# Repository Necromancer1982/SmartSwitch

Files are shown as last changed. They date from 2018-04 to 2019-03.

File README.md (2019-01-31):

# SmartSwitch
## Flush-mounted Module to control shutters / realize an intermediate switch with ESP8266

**Version History**

- SmartSwitch V1.2  04/2018   1st official public Version
- SmartSwitch V1.3  05/2018   ADD: Additional Fuse (F2, 4A) for consumer current
- **Software now avaliable for ArduinoIDE (including OTA)**

**Vision**

During the construction of our new house, we’ve decided to install motorized roller shutters. To control them, we first used only standard shutter-push-buttons, right beside the correspondent window. As second step a *smart solution* should be established.

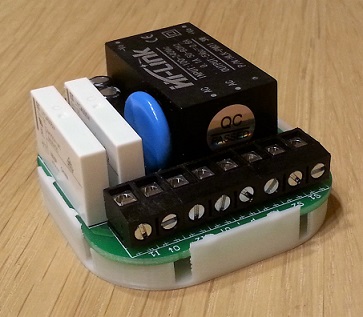
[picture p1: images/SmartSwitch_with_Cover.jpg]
SmartSwitch Modul
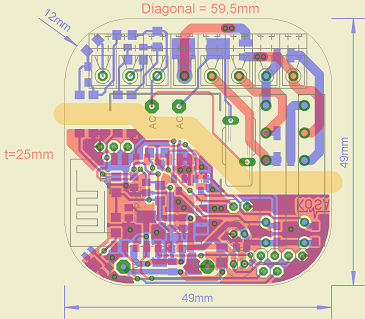
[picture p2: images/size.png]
SmartSwitch Sizing
   

Inspired by Leo-Andres Hofmann’s “230V I/O Modul für ESP8266” ([LUANI](https://luani.de/projekte/esp8266-hvio/)), I’ve decided to develop my own module to sense the shutter-push-buttons and control the motorization.
By its dimensions, the module perfectly fits into a standard round In-Wall-Pattress (inner diameter: 60mm). If its a so called "deep" pattress, the shutter-push-buttons can also be installed on top of the module and there is enough space left for wires and terminals.

Basis of the module is a ESP-12F, an integrated WLAN-Module which controls two changeover relays to move the shutters. 

The operation of the module can either be controlled by the already existing push-buttons, or via MQTT-Messages by WLAN, central controlled via [OpenHab2](https://docs.openhab.org/index.html), running on my Raspberry Pi Zero W. Therefore, a movement of the shutters regarding time or special events, for example time of dusk and down ([Astro Bindings](https://docs.openhab.org/addons/bindings/astro/readme.html)) can be realized. Also an automatized shadowing regarding sun position, global radiation and inside / outside temperature will be possible.

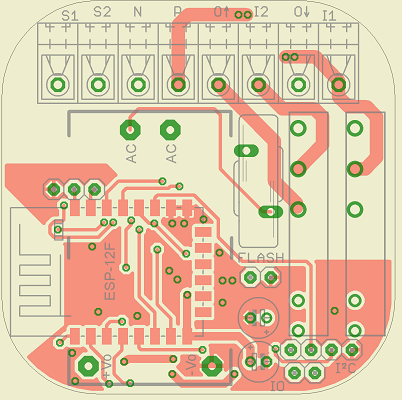
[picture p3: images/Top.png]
PCB Top
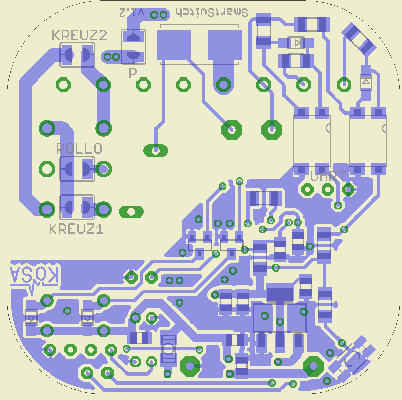
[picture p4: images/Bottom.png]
PCB Bottom
   

**Hardware**

Beside the WLAN-Module and the relays (contact rating 1500VA, 6A/250V), a power supply consisting of a AC/DC-Converter HI-Link HLK-PM01 (5V/600mA) to serve the relays and a voltage regulator TS1117 (LowDrop 3V) to serve the remaining circuit, a 2-chanel power sense circuit to detect 230V levels for the controller and interfaces like UART, I²C and analog/digital IO are included on the board. A push button for hardware reset is also implemented on bottom side of the PCB.

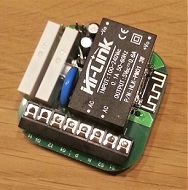
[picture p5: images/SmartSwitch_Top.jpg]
SmartSwitch Modul
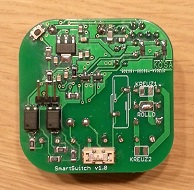
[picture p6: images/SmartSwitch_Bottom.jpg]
SmartSwitch Modul
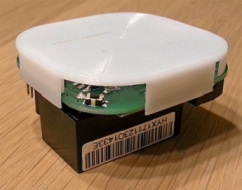
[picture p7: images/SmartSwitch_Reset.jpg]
SmartSwitch Modul
          

Three soldering jumpers give the opportunity to decide if the relays should act as an intermediate switch to implement the module in an already existing light-installation or to act as a roller-shutter-controlling device. Therefore, the first relay powers the motor during the second relay controls moving direction. Via a fourth soldering Jumper it is possible to supply mains voltage to the relays, so for roller shutter function, there is no need to connect phase two times, for supplying the module and supplying the motor. 

The power supply of the module is secured by a SMD-Fuse (500mA) and a varistor (275V) against overload.

**Software**

In addition to the firmware ([NodeMCU](https://nodemcu.readthedocs.io/en/master/)) there are mainly four LUA-Scripts on the Module.

The Init-File tries to connect to the access point whose SSID and password is stored at the ESP. If the connection couldn’t be established, the ESP himself opens an access point and starts an end user setup to give the user the possibility to enter SSID and password of an already existing access point (Router).

If the connection is established, two more software modules will be started. The MQTT-Module starts to configure the implemented MQTT-Client, opens a connection to the MQTT-Broker which is defined (IP, Port) in the MQTT.ini file and provides several procedures for MQTT communication. The INI-Handling-Module provides two more procedures for easy INI-File access by using “Key” and “Value” data.

Finally, the main program will be started.

:+1: _UPDATE_

Now I'd also written a new software for ArduinoIDE.
The main advantage of this new sketch is the possibility of updating the software via OTA (Over the Air update via WiFi).
After flashing the sketch via serial adapter for the first time, the module can be found and flashed via ArduinoIDE OTA-Functionality.

Additionally there are a few smaller upgrades and BugFixes implemented in the new software.

The functionality of the Arduino-Software is mostly the same as the LUA-Skript.
The module tries to connect to the last stored access point. If no connection could be established the module starts its implemented enduser setup. SSID and password of the AP and also the site of usage and MQTT-borker IP can be configured. After this initialisation the module starts its normal operation and can be either controlled via the already existing push buttons or MQTT-Commands.

**Function**

During normal operation, the main program offers the opportunity to control the module via the shutter-push-buttons by using both of the power sense inputs. (Only LUA-Skript: If both buttons were pushed synchronously the module changes to teaching mode.) Via MQTT-Command "TEACH", the module changes to teaching mode. Because of the fact that simple shutter motors neither feedback their position nor the state of their limit switches, the position of the shutter can only be traced by the time, the motor is in motion. Therefore, in teaching mode, the time to reach both final positions can be stored in module by closing and reopening the shutter completely.
After that, a short push of a button results in moving to respective end position. If the button will be pressed longer then 1s the shutter moves as long as the button is pressed or final position is reached. By releasing the button, the current position of the shutter will be calculated regarding the time, the motor was in motion and will be stored in the module. Thus offers the opportunity to start motion from any position of the shutter or moving the shutter to a particular position (e.g. closing until only shutter slots are open).

But not only manual operation by pushing a button is possible. As mentioned, the module acts also as a MQTT-Client. Via messages to the MQTT-Topic (LUA-Skript: which is also settled in MQTT.ini file; ARDUINO-Skript: /SmartSwitch/SmartSwitch_\<SITE or MAC\>/), motion to the final position is possible, either by command “UP” or “DOWN”. By sending a value from 0 to 100 the shutter moves to the correspondent position in percent. If the desired position is reached or the shutter reaches end position, the current position will be also send as MQTT-Message to the broker (ARDUINO: Also the RSSI of the module will be sent). Therefore, a visualization of the current position e.g. with  [HabPanel von OpenHab](https://docs.openhab.org/addons/uis/habpanel/readme.html) is possible.

**Safety**

By operating the module at mains voltage, the active parts and pins should be covered against directly and indirectly touching. Therefore, I’ve designed a Bottom-Coverage ([Project at Thingiverse](https://www.thingiverse.com/thing:3085953)) for the module with FreeCAD and printed it with my Anet A6 3D-Printer. As positive side effect of the coverage, all SMT-Components on bottom side are protected against mechanical damages.

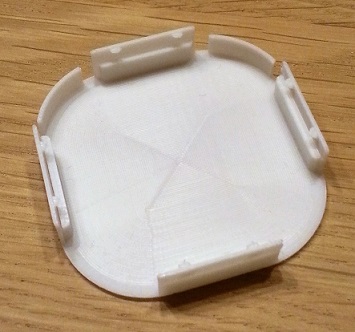
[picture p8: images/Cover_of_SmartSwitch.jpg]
SmartSwitch Modul


### Safety Disclaimer

Building and usage at your own risk. SmartSwitch uses potentially lethal mains voltages.

If you are a beginner in electronics or don't have the proper experience to work with mains voltage, consult a professional! I am not liable for any mishaps that may occur due to misuse of SmartSwitch or electrical system (including mains power) including but not limited to: errors or omissions, loss of life, or property damage. Take all safety precautions as necessary. You are fully responsible for your actions, perform them at your own risk!

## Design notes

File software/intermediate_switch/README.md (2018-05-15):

# SmartSwitch
## Flush-mounted Module to control shutters / realize an intermediate switch with ESP8266

# Software for intermediate switch under construction!

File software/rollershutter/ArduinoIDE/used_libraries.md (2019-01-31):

## Used Libraries for ArduinoIDE

| Library | Link |
|---|---|
| ESP8266WiFi.h | [https://github.com/esp8266/Arduino/tree/master/libraries/ESP8266WiFi](https://github.com/esp8266/Arduino/tree/master/libraries/ESP8266WiFi) |
| WiFiClient.h | [https://github.com/esp8266/Arduino/tree/master/libraries/ESP8266WiFi](https://github.com/esp8266/Arduino/tree/master/libraries/ESP8266WiFi) |
| EEPROM.h | [https://github.com/esp8266/Arduino/tree/master/libraries](https://github.com/esp8266/Arduino/tree/master/libraries) |
| WiFiManager.h | [https://github.com/tzapu/WiFiManager](https://github.com/tzapu/WiFiManager) |
| ArduinoOTA.h | [https://github.com/esp8266/Arduino/tree/master/libraries](https://github.com/esp8266/Arduino/tree/master/libraries) |
| ESP8266mDNS.h | [https://github.com/esp8266/Arduino/tree/master/libraries](https://github.com/esp8266/Arduino/tree/master/libraries) |
| WiFiUdp.h | [https://github.com/esp8266/Arduino/tree/master/libraries/ESP8266WiFi](https://github.com/esp8266/Arduino/tree/master/libraries/ESP8266WiFi)|
| PubSubClient.h | [https://github.com/knolleary/pubsubclient](https://github.com/knolleary/pubsubclient)|
| user_interface.h | [https://github.com/esp8266/Arduino/tree/master/tools/sdk/include](https://github.com/esp8266/Arduino/tree/master/tools/sdk/include)|

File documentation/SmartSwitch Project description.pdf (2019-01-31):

# SmartSwitch

## Flush-mounted Module to control shutters / realize an intermediate switch with ESP8266

Version History

- SmartSwitch V1.2 04/2018 1st official public Version
- SmartSwitch V1.3 05/2018 ADD: Additional Fuse (F2, 4A) for consumer current
- Software now avaliable for ArduinoIDE (including OTA)

Vision

During the construction of our new house, we’ve decided to install motorized roller shutters. To control them, we first used only standard shutter-push-buttons, right beside the correspondent window. As second step a smart solution should be established.

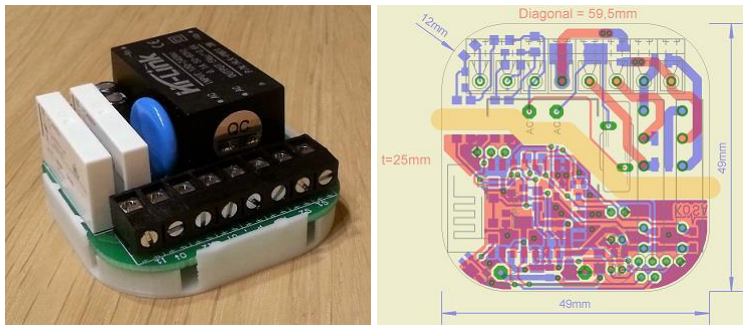
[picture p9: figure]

Inspired by Leo-Andres Hofmann’s “230V I/O Modul für ESP8266” (LUANI), (https://luani.de/projekte/esp8266-hvio/) I’ve decided to develop my own module to sense the shutter-push-buttons and control the motorization. By its dimensions, the module perfectly fits into a standard round In-Wall-Pattress (inner diameter: 60mm). If its a so called "deep" pattress, the shutterpush-buttons can also be installed on top of the module and there is enough space left for wires and terminals.

Basis of the module is a ESP-12F, an integrated WLAN-Module which controls two changeover relays to move the shutters.

The operation of the module can either be controlled by the already existing push-buttons, or via MQTT-Messages by WLAN, central controlled via OpenHab2, (https://docs.openhab.org/index.html) running on my Raspberry Pi Zero W. Therefore, a movement of the shutters regarding time or special events, for example time of dusk and down (Astro Bindings) (https://docs.openhab.org/addons/bindings/astro/readme.html) can be realized.

Also an automatized shadowing regarding sun position, global radiation and inside / outside temperature will be possible.

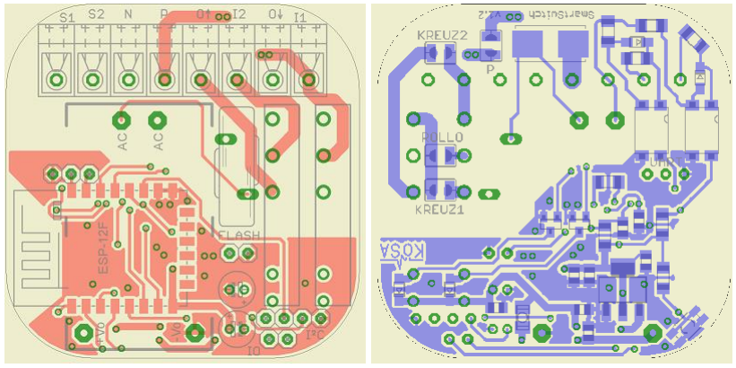
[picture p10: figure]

Hardware

Beside the WLAN-Module and the relays (contact rating 1500VA, 6A/250V), a power supply consisting of a AC/DC-Converter HI-Link HLK-PM01 (5V/600mA) to serve the relays and a voltage regulator TS1117 (LowDrop 3V) to serve the remaining circuit, a 2-chanel power sense circuit to detect 230V levels for the controller and interfaces like UART, I²C and analog/digital IO are included on the board. A push button for hardware reset is also implemented on bottom side of the PCB.

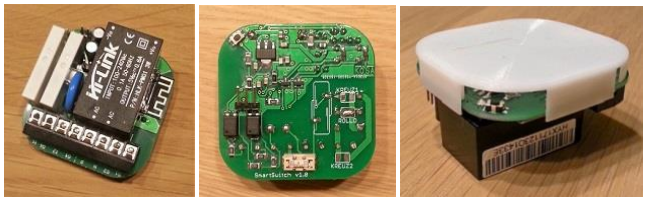
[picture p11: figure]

Three soldering jumpers give the opportunity to decide if the relays should act as an intermediate switch to implement the module in an already existing light-installation or to act as a roller-shutter-controlling device. Therefore, the first relay powers the motor during the second relay controls moving direction. Via a fourth soldering Jumper it is possible to supply mains voltage to the relays, so for roller shutter function, there is no need to connect phase two times, for supplying the module and supplying the motor.

The power supply of the module is secured by a SMD-Fuse (500mA) and a varistor (275V) against overload.

Software

In addition to the firmware (NodeMCU) (https://nodemcu.readthedocs.io/en/master/) there are mainly four LUA-Scripts on the Module.

The Init-File tries to connect to the access point whose SSID and password is stored at the ESP. If the connection couldn’t be established, the ESP himself opens an access point and starts an end user setup to give the user the possibility to enter SSID and password of an already existing access point (Router).

If the connection is established, two more software modules will be started. The MQTT-Module starts to configure the implemented MQTT-Client, opens a connection to the MQTT-Broker which is defined (IP, Port) in the MQTT.ini file and provides several procedures for MQTT communication. The INI-Handling-Module provides two more procedures for easy INI-File access by using “Key” and “Value” data.

Finally, the main program will be started.

👍 UPDATE

Now I'd also written a new software for ArduinoIDE. The main advantage of this new sketch is the possibility of updating the software via OTA (Over the Air update via WiFi). After flashing the sketch via serial adapter for the first time, the module can be found and flashed via ArduinoIDE OTA-Functionality.

Additionally there are a few smaller upgrades and BugFixes implemented in the new software.

The functionality of the Arduino-Software is mostly the same as the LUA-Skript. The module tries to connect to the last stored access point. If no connection could be established the module starts its implemented enduser setup. SSID and password of the AP and also the site of usage and MQTT-borker IP can be configured. After this initialisation the module starts its normal operation and can be either controlled via the already existing push buttons or MQTT-Commands.

Function

During normal operation, the main program offers the opportunity to control the module via the shutter-push-buttons by using both of the power sense inputs. (Only LUA-Skript: If both buttons were pushed synchronously the module changes to teaching mode.) Via MQTT-Command "TEACH", the module changes to teaching mode. Because of the fact that simple shutter motors neither feedback their position nor the state of their limit switches, the position of the shutter can only be traced by the time, the motor is in motion. Therefore, in teaching mode, the time to reach both final positions can be stored in module by closing and reopening the shutter completely. After that, a short push of a button results in moving to respective end position. If the button will be pressed longer then 1s the shutter moves as long as the button is pressed or final position is reached. By releasing the button, the current position of the shutter will be calculated regarding the time, the motor was in motion and will be stored in the module. Thus offers the opportunity to start motion from any position of the shutter or moving the shutter to a particular position (e.g. closing until only shutter slots are open).

But not only manual operation by pushing a button is possible. As mentioned, the module acts also as a MQTT-Client. Via messages to the MQTT-Topic (LUA-Skript: which is also settled in MQTT.ini file; ARDUINO-Skript: /SmartSwitch/SmartSwitch_<SITE or MAC>/), motion to the final position is possible, either by command “UP” or “DOWN”. By sending a value from 0 to 100 the shutter moves to the correspondent position in percent. If the desired position is reached or the shutter reaches end position, the current position will be also send as MQTT-Message to the broker (ARDUINO: Also the RSSI of the module will be sent). Therefore, a visualization of the current position e.g. with HabPanel von OpenHab (https://docs.openhab.org/addons/uis/habpanel/readme.html) is possible.

Safety

By operating the module at mains voltage, the active parts and pins should be covered against directly and indirectly touching. Therefore, I’ve designed a Bottom-Coverage for the module with FreeCAD and printed it with my Anet A6 3D-Printer. As positive side effect of the coverage, all SMT-Components on bottom side are protected against mechanical damages.

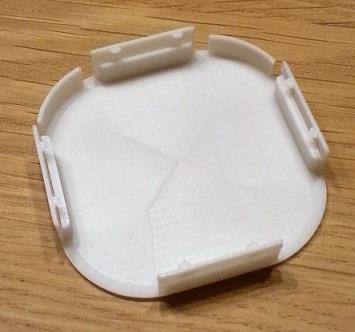
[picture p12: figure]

### Safety Disclaimer

Building and usage at your own risk. SmartSwitch uses potentially lethal mains voltages.

If you are a beginner in electronics or don't have the proper experience to work with mains voltage, consult a professional! I am not liable for any mishaps that may occur due to misuse of SmartSwitch or electrical system (including mains power) including but not limited to: errors or omissions, loss of life, or property damage. Take all safety precautions as necessary. You are fully responsible for your actions, perform them at your own risk!

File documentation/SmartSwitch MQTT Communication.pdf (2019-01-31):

# SmartSwitch MQTT-Communication

## MQTT-Topics:

Topic to send commands to module:
LUA-Script: | /SmartSwitch/<MAC>/command
ARDUINO-Script: /SmartSwitch/SmartSwitch_<SITE or MAC>/command

Topic, the module feedbacks position / RSSI to:
LUA-Script: | /SmartSwitch/<MAC>/status
ARDUINO-Script: /SmartSwitch/SmartSwitch_<SITE or MAC>/status/position /SmartSwitch/SmartSwitch_<SITE or MAC>/status/rssi

## MQTT-Commands:

UP
Opens roller shutter completely and feedbacks position (0) when end position is reached

DOWN
Closes roller shutter completely and feedbacks position (100) when end position is reached

STOP
Stops moving roller shutter and feedbacks current position

[Integer: 0 – 100]
Moves roller shutter to the integer related position in percent and feedbacks reached position

STATUS
Feedbacks current position of roller shutter

TEACH
Sets Module in teaching mode; Moving to lower end position, followed by moving to upper end position, by pressing manual roller shutter buttons, stores time for up-/down-movement into the module

MANUAL_START
Starts “Position-Repair-Mode”; Movement of roller shutter by pressing manual roller shutter buttons is now possible, without storage of position in module after stopping

MAUAL_STOP
Stops “Position-Repair-Mode”

## MQTT-Setup:

Quality of Service Level: | 1
Retain active: | no
Secure active: | no
Keep-alive Time: | 120s

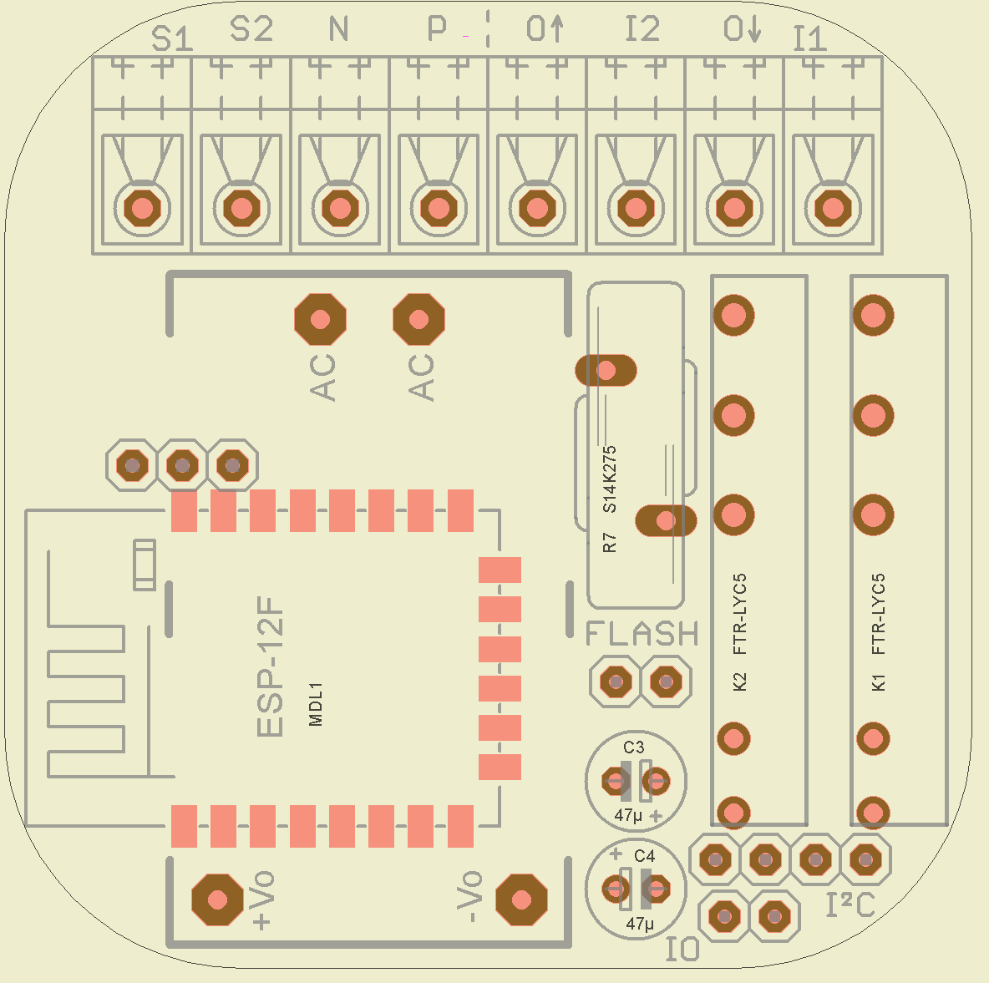
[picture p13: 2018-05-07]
hardware/v1.3/Placing_Top_V1_3.png

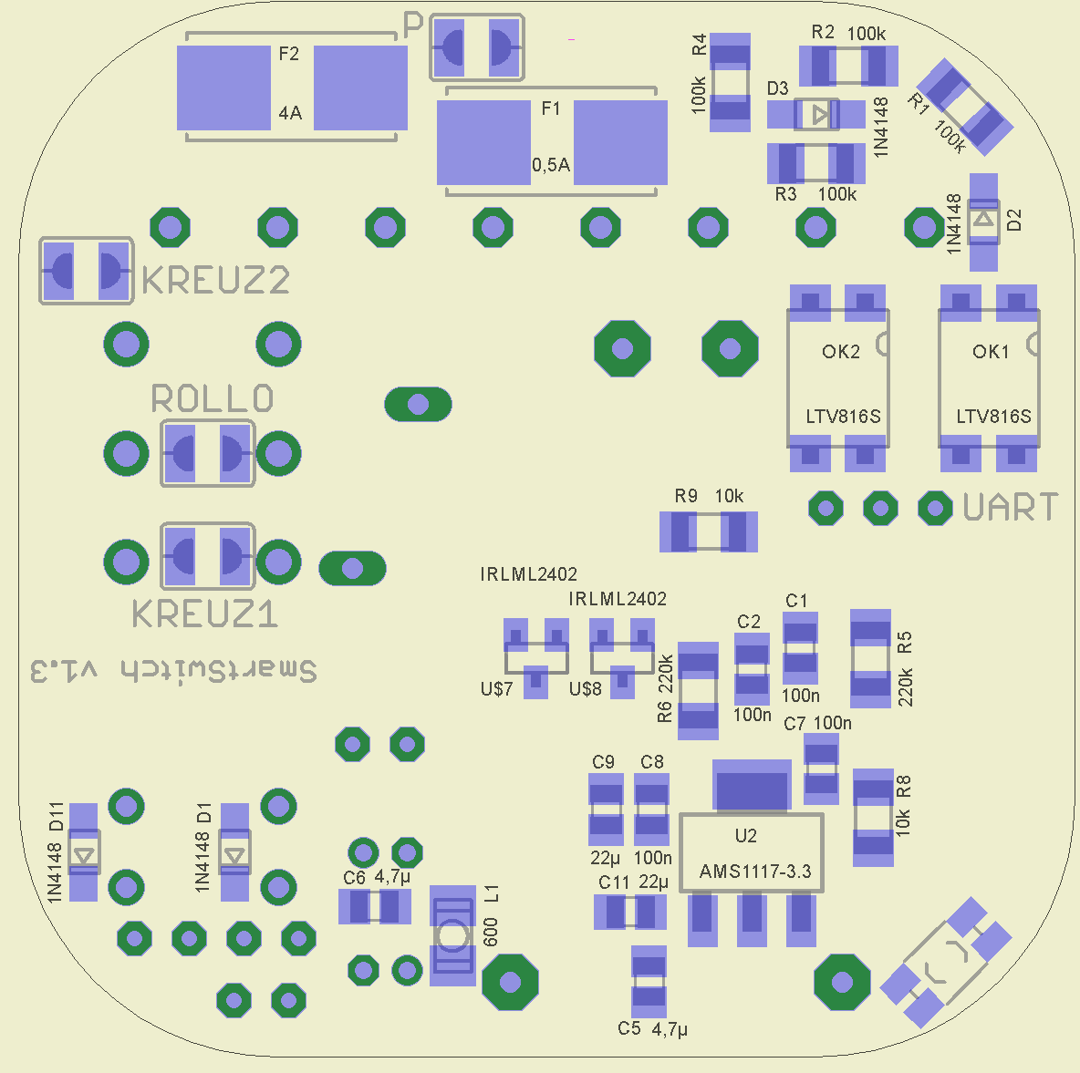
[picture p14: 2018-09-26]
hardware/v1.3/Placing_Bottom_V1_3.png

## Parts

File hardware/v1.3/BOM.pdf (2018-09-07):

Device | Parts | Alternative
1 | PCB | 1,22 € | 1,22 €
1 | SMD-HASF 0,5A | F1 | 0,99 € | 0,99 €
1 | SMD-HASF 4,0A | F2 | 0,99 € | 0,99 €
1 | MDL1 | 3,85 € | 3,85 € | 1,49 €
4 | RND 1206 1 100K | R1, R2, R3, R4 | 0,02 € | 0,08 €
4 | KEM X7R0805 100N | C1, C2, C7, C8 | 0,02 € | 0,08 €
2 | RND 1206 1 10K | R8, R9 | 0,02 € | 0,04 €
4 | 1N 4148 WS | D1, D11 | 0,03 € | 0,12 €
2 | RND 205-00632 | FLASH, IO | 0,05 € | 0,10 €
2 | X5R-G0805 22/6 | C9, C11 | 0,07 € | 0,14 €
1 | RND 205-00624 | UART | 0,11 € | 0,11 €
1 | RND 205-00625 | I²C | 0,08 € | 0,08 €
2 | X7R 0805 CC 4,7U | C5, C6 | 0,04 € | 0,08 €
2 | RND 1206 1 220K | R5, R6 | 0,02 € | 0,04 €
2 | RAD FR 47/25 | C3, C4 | 0,14 € | 0,28 €
1 | BLM31PG 601 | L1 | 0,22 € | 0,22 €
1 | TS 1117 BCW33 | U2 | 0,32 € | 0,32 €
2 | FTR LYCA 005V | K1, K2 | 1,90 € | 3,80 €
1 | Amazon U$1 | 3,98 € | 3,98 € | 1,87 €
2 | IRLML 2402 | U$7, U$8 | 0,16 € | 0,32 €
2 | LTV 816S | OK1, OK2 | 0,22 € | 0,44 €
1 | RND 205-00282 | U$2, U$3, U$4, U$5 | 0,96 € | 0,96 €
1 | VDR-0,6 270 | R7 | 0,21 € | 0,21 €
1 | KMR 231 G LFS | RST | 0,25 € | 0,25 €
17,48 € | 13,24 €

# BOM SmartSwitch V1.3

Qty | Order Number | Supplier | Unit Price | Sum Price
PCB (https://www.itead.cc/open-pcb/pcb-prototyping/2layer-green-pcb-5cm-x-5cm-max.html) | Itead
SMD-HASF 0,5A (SMT-Sicherung inkl. Halter) (https://www.reichelt.de/SMD-Sicherungen/SMD-HASF-0-5A/3/index.html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) | Reichelt
SMD-Sicherung mit Halter, superflink, 4,0A (https://www.reichelt.de/SMD-Sicherungen/SMD-HASF-4-0A/3/index.html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) | Reichelt
AI-Thinker ESP8266 ESP-12F WiFi/WLAN Modul (http://www.watterott.com/de/ESP8266-ESP-12F-WiFi/WLAN-Modul) | Waterott | Aliexpress
SMD-Widerstand, 1206, 100 kOhm, 250 mW, 1% (https://www.reichelt.de/SMD-1206-von-1-bis-910-kOhm/RND-1206-1-100K/3/index.html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) | Reichelt
Vielschicht-Kerko, 100nF, 50V, 125°C (https://www.reichelt.de/Vielschicht-SMD-G0805/KEM-X7R0805-100N/3/index.html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) | Reichelt
SMD-Widerstand, 1206, 10 kOhm, 250 mW, 1% (https://www.reichelt.de/SMD-1206-von-1-bis-910-kOhm/RND-1206-1-10K/3/index.html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) | Reichelt
SMD-Si-Allzweckdioden, SOD323F, 75V, 0,15A (https://www.reichelt.de/1N-UF-AA-Dioden/1N-4148-WS/3/index.html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) | Reichelt
RND Stiftleiste, 2-pol, RM 2,54 mm (https://www.reichelt.de/Stiftleisten/RND-205-00632/3/index.html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) | Reichelt
SMD-Vielschichtkondensator G0805 - 22µF 6,3V (https://www.reichelt.de/Vielschicht-SMD-G0805/X5R-G0805-22-6/3/index.html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) | Reichelt
RND Stiftleiste, 3-pol, RM 2,54 mm (https://www.reichelt.de/Stiftleisten/RND-205-00624/3/index.html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) | Reichelt
RND Stiftleiste, 4-pol, RM 2,54 mm (https://www.reichelt.de/Stiftleisten/RND-205-00625/3/index.html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) | Reichelt
SMD-Kerko, 0805, 4,7µF, 10V, 10%, MLCC (https://www.reichelt.de/Vielschicht-SMD-G0805/X7R-0805-CC-4-7U/3/index.html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) | Reichelt
SMD-Widerstand, 1206, 220 kOhm, 250 mW, 1% (https://www.reichelt.de/RND-1206-1-220K/3/index.html?ACTION=3&LA=55&ARTICLE=183413) | Reichelt
Elko radial, 47 uF, 25 V, 105°C, low ESR (https://www.reichelt.de/Elkos-radial-105-C-5000-10000h/RAD-FR-47-25/3/index.html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) | Reichelt
EMI Suppression Filter SMD1206 BLM31 600 Ohm (https://www.reichelt.de/Filter/BLM31PG-601/3/index.html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) | Reichelt
LDO-U-Reg 3,3V 0,8A SOT223 (https://www.reichelt.de/ICs-TLC-TSA-/TS-1117-BCW33/3/index.html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) | Reichelt
Schmales Netzrelais FTR-LYCA, 5V, 1 We., 6A (https://www.reichelt.de/Print-Steckrelais/FTR-LYCA-005V/3/index.html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) | Reichelt
HI-Link HLK-PM01 AC-DC (https://www.amazon.de/HI-Link-HLK-PM01-Step-Down-Netzteil-Intelligent/dp/B01768OJMS) | Aliexpress
SMD-MOSFET, N-LogL, SOT23, 20V, 1.2A (https://www.reichelt.de/IRL-IRFZ-Transistoren/IRLML-2402/3/index.html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) | Reichelt
Optokoppler 5kV 80V 50mA >50% SMD (https://www.reichelt.de/Optokoppler/LTV-816S/3/index.html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) | Reichelt
Lötbare Schraubklemme - 8-pol, RM 5 mm, 0° (https://www.reichelt.de/RND-connect/RND-205-00282/3/index.html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) | Reichelt
Varistor,Rm 7,5mm, 0,6W, 275VAC (https://www.reichelt.de/Heissleiter-Varistoren/VDR-0-6-270/3/index.html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) | Reichelt
SMD-Kurzhubtaster, 4,2 x 2,8 mm, Höhe 1,9 mm (https://www.reichelt.de/Kurzhubtaster/KMR-231-G-LFS/3/index.html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) | Reichelt

Reichelt Order list (https://www.reichelt.de/my/1501969)

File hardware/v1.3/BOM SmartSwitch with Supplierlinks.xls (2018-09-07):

BOM SmartSwitch V1.3
Qty | Device | Order Number | Supplier | Parts | Unit Price | Sum Price | Alternative
1 | PCB (https://www.itead.cc/open-pcb/pcb-prototyping/2layer-green-pcb-5cm-x-5cm-max.html) |  | Itead | PCB | 1.22 € | 1.22 €
1 | SMD-HASF 0,5A (SMT-Sicherung inkl. Halter) (https://www.reichelt.de/SMD-Sicherungen/SMD-HASF-0-5A/3/index.html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) | SMD-HASF 0,5A | Reichelt | F1 | 0.99 € | 0.99 €
1 | SMD-Sicherung mit Halter, superflink, 4,0A (https://www.reichelt.de/SMD-Sicherungen/SMD-HASF-4-0A/3/index.html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) | SMD-HASF 4,0A | Reichelt | F2 | 0.99 € | 0.99 €
1 | AI-Thinker ESP8266 ESP-12F WiFi/WLAN Modul (http://www.watterott.com/de/ESP8266-ESP-12F-WiFi/WLAN-Modul) |  | Waterott | MDL1 | 3.85 € | 3.85 € | 1.49 € | Aliexpress
4 | SMD-Widerstand, 1206, 100 kOhm, 250 mW, 1% (https://www.reichelt.de/SMD-1206-von-1-bis-910-kOhm/RND-1206-1-100K/3/index.html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) | RND 1206 1 100K | Reichelt | R1, R2, R3, R4 | 0.02 € | 0.08 €
4 | Vielschicht-Kerko, 100nF, 50V, 125°C (https://www.reichelt.de/Vielschicht-SMD-G0805/KEM-X7R0805-100N/3/index.html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) | KEM X7R0805 100N | Reichelt | C1, C2, C7, C8 | 0.02 € | 0.08 €
2 | SMD-Widerstand, 1206, 10 kOhm, 250 mW, 1% (https://www.reichelt.de/SMD-1206-von-1-bis-910-kOhm/RND-1206-1-10K/3/index.html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) | RND 1206 1 10K | Reichelt | R8, R9 | 0.02 € | 0.04 €
4 | SMD-Si-Allzweckdioden, SOD323F, 75V, 0,15A (https://www.reichelt.de/1N-UF-AA-Dioden/1N-4148-WS/3/index.html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) | 1N 4148 WS | Reichelt | D1, D11 | 0.03 € | 0.12 €
2 | RND Stiftleiste, 2-pol, RM 2,54 mm (https://www.reichelt.de/Stiftleisten/RND-205-00632/3/index.html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) | RND 205-00632 | Reichelt | FLASH, IO | 0.05 € | 0.10 €
2 | SMD-Vielschichtkondensator G0805 - 22µF 6,3V (https://www.reichelt.de/Vielschicht-SMD-G0805/X5R-G0805-22-6/3/index.html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) | X5R-G0805 22/6 | Reichelt | C9, C11 | 0.07 € | 0.14 €
1 | RND Stiftleiste, 3-pol, RM 2,54 mm (https://www.reichelt.de/Stiftleisten/RND-205-00624/3/index.html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) | RND 205-00624 | Reichelt | UART | 0.11 € | 0.11 €
1 | RND Stiftleiste, 4-pol, RM 2,54 mm (https://www.reichelt.de/Stiftleisten/RND-205-00625/3/index.html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) | RND 205-00625 | Reichelt | I²C | 0.08 € | 0.08 €
2 | SMD-Kerko, 0805, 4,7µF, 10V, 10%, MLCC (https://www.reichelt.de/Vielschicht-SMD-G0805/X7R-0805-CC-4-7U/3/index.html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) | X7R 0805 CC 4,7U | Reichelt | C5, C6 | 0.04 € | 0.08 €
2 | SMD-Widerstand, 1206, 220 kOhm, 250 mW, 1% (https://www.reichelt.de/RND-1206-1-220K/3/index.html?ACTION=3&LA=55&ARTICLE=183413) | RND 1206 1 220K | Reichelt | R5, R6 | 0.02 € | 0.04 €
2 | Elko radial, 47 uF, 25 V, 105°C, low ESR (https://www.reichelt.de/Elkos-radial-105-C-5000-10000h/RAD-FR-47-25/3/index.html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) | RAD FR 47/25 | Reichelt | C3, C4 | 0.14 € | 0.28 €
1 | EMI Suppression Filter SMD1206 BLM31 600 Ohm (https://www.reichelt.de/Filter/BLM31PG-601/3/index.html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) | BLM31PG 601 | Reichelt | L1 | 0.22 € | 0.22 €
1 | LDO-U-Reg 3,3V 0,8A SOT223 (https://www.reichelt.de/ICs-TLC-TSA-/TS-1117-BCW33/3/index.html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) | TS 1117 BCW33 | Reichelt | U2 | 0.32 € | 0.32 €
2 | Schmales Netzrelais FTR-LYCA, 5V, 1 We., 6A (https://www.reichelt.de/Print-Steckrelais/FTR-LYCA-005V/3/index.html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) | FTR LYCA 005V | Reichelt | K1, K2 | 1.90 € | 3.80 €
1 | HI-Link HLK-PM01 AC-DC (https://www.amazon.de/HI-Link-HLK-PM01-Step-Down-Netzteil-Intelligent/dp/B01768OJMS) |  | Amazon | U$1 | 3.98 € | 3.98 € | 1.87 € | Aliexpress
2 | SMD-MOSFET, N-LogL, SOT23, 20V, 1.2A (https://www.reichelt.de/IRL-IRFZ-Transistoren/IRLML-2402/3/index.html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) | IRLML 2402 | Reichelt | U$7, U$8 | 0.16 € | 0.32 €
2 | Optokoppler 5kV 80V 50mA >50% SMD (https://www.reichelt.de/Optokoppler/LTV-816S/3/index.html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) | LTV 816S | Reichelt | OK1, OK2 | 0.22 € | 0.44 €
1 | Lötbare Schraubklemme - 8-pol, RM 5 mm, 0° (https://www.reichelt.de/RND-connect/RND-205-00282/3/index.html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) | RND 205-00282 | Reichelt | U$2, U$3, U$4, U$5 | 0.96 € | 0.96 €
1 | Varistor,Rm 7,5mm, 0,6W, 275VAC (https://www.reichelt.de/Heissleiter-Varistoren/VDR-0-6-270/3/index.html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) | VDR-0,6 270 | Reichelt | R7 | 0.21 € | 0.21 €
1 | SMD-Kurzhubtaster, 4,2 x 2,8 mm, Höhe 1,9 mm (https://www.reichelt.de/Kurzhubtaster/KMR-231-G-LFS/3/index.html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) | KMR 231 G LFS | Reichelt | RST | 0.25 € | 0.25 €
 | Reichelt Order list (https://www.reichelt.de/my/1501969) |  |  |  |  | 17.48 € | 13.24 €

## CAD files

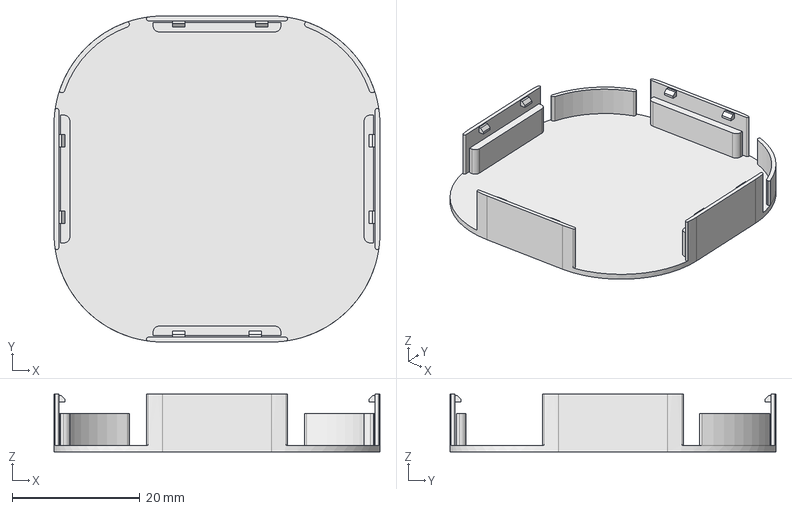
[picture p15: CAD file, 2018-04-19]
Coverage 3D-Files/SmartSwitch2.FCStd
51.0 x 51.0 x 9.00 mm

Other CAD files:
Coverage 3D-Files/SmartSwitch 2.obj
Coverage 3D-Files/SmartSwitch2.stl

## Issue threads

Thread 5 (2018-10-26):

Platinen oder Gerber Files?

Tommy-LSA, 2018-10-26:
Hallo,
Ist es möglich, 10 Platinen zu bekommen, oder die Gerber Files um selbst welche bei itead.cc zu ordern? Ich würde gerne unsere Rolläden im Haus über Tasmota und FHEM steuern. Du scheinst der Einzige zu sein, der eine passende Hardware entwickelt hat. Ich komme eher aus der Software Ecke und habe mit Platinen (erstellen/bestellen) nicht viel am Hut. Das Löten traue ich mir noch zu, anhand Deiner sehr guten Dokumentation.
Danke, das Du das Projekt veröffentlicht hast.

leschNUX, 2018-10-27:
Hi,

Ich hab noch welche, wenn du mir deine Mailadresse schickst, kann ich dir welche schicken!

Tommy-LSA, 2018-10-27:
Oh, das wär super. Mailadresse ist: pirat(im)stadtweg(in)de

Necromancer1982, 2018-11-08:
Hi,
sorry, war im Urlaub und damit länger nicht mehr auf GitHub...
Die CAM-Files sind bereits im Repo.
Mit diesen kannst du direkt bei itead bestellen.

Gruß Andreas

Closed 2018-11-08.

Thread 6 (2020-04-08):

Relais Time - Motion Stop

painkiller996699, 2020-04-08:
The order in the "motionStop()" method of the "digitalWrite()" commands is reversed.

First the power relay should go off and then the relay for the direction. In the code it is reversed. This has the side effect that a small voltage pulse is always passed on when stopping the movement.

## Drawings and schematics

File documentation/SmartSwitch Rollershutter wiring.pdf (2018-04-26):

# Wiring of SmartSwitch as roller shutter control

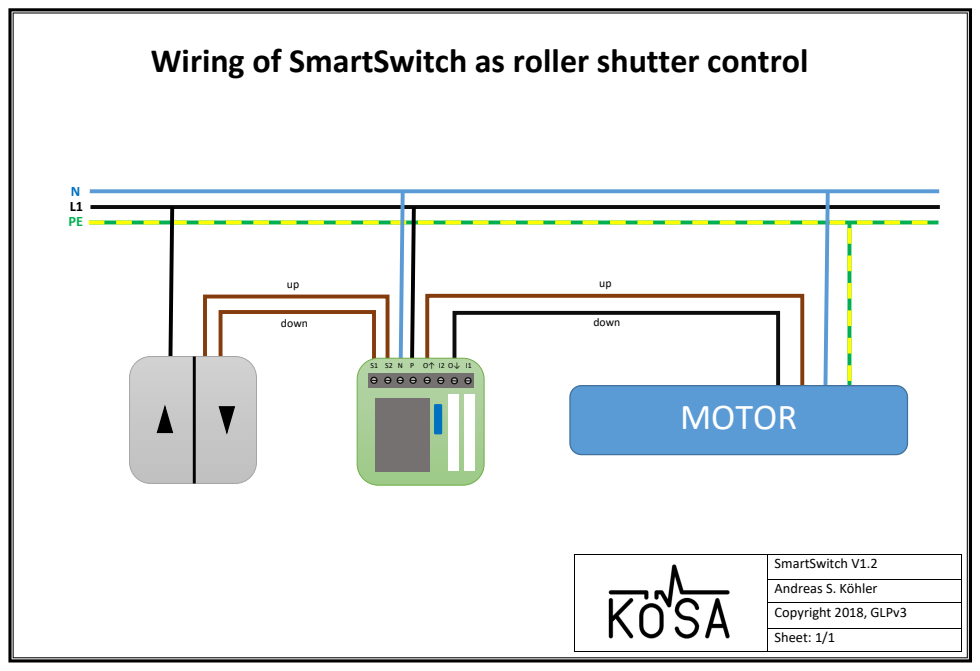
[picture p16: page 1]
MOTOR; down; SmartSwitch V1.2; Andreas S. Köhler; Copyright 2018, GLPv3; Sheet: 1/1

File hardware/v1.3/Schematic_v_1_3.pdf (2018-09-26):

# Spannungsversorgung

# Relaisschaltung

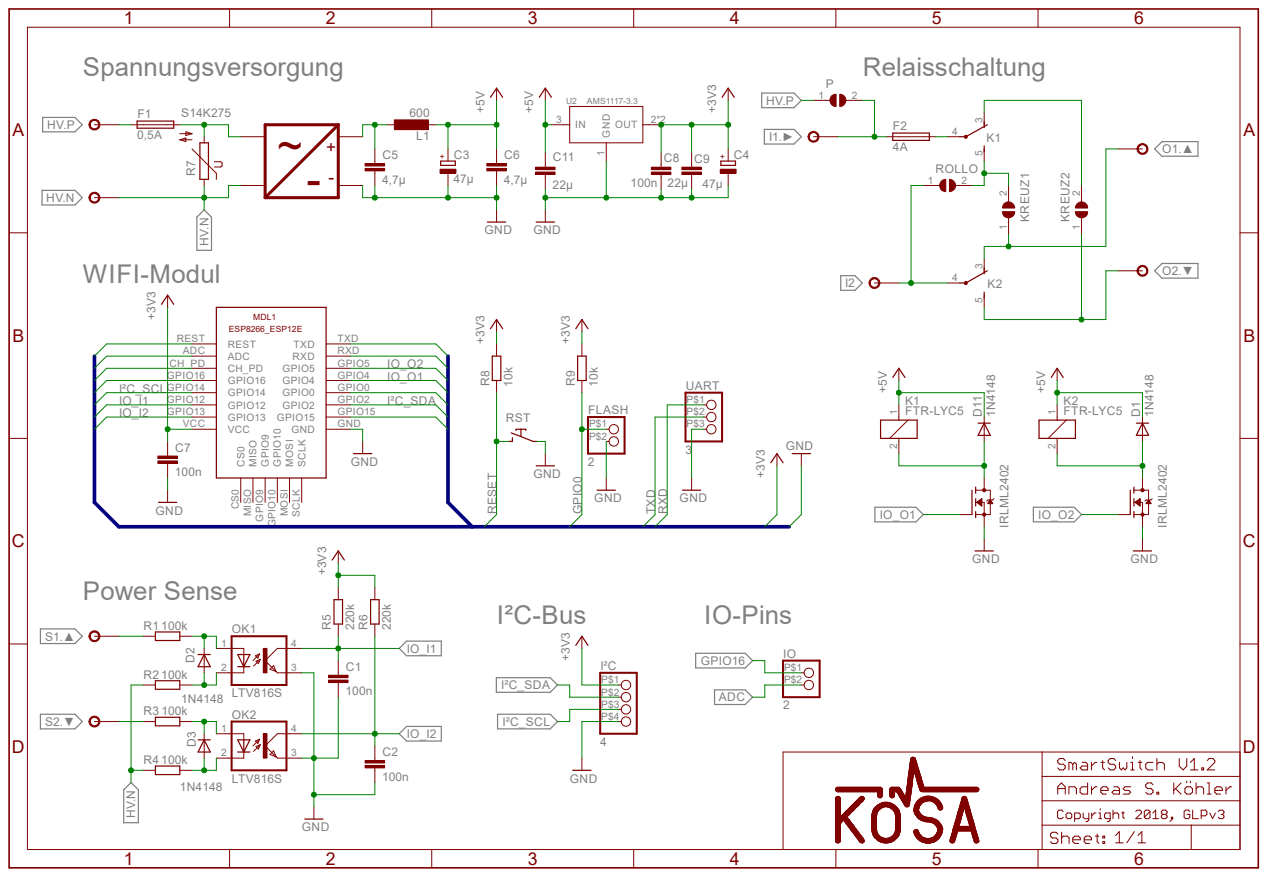
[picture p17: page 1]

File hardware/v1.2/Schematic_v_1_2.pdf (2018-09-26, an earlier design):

# Spannungsversorgung

# Relaisschaltung

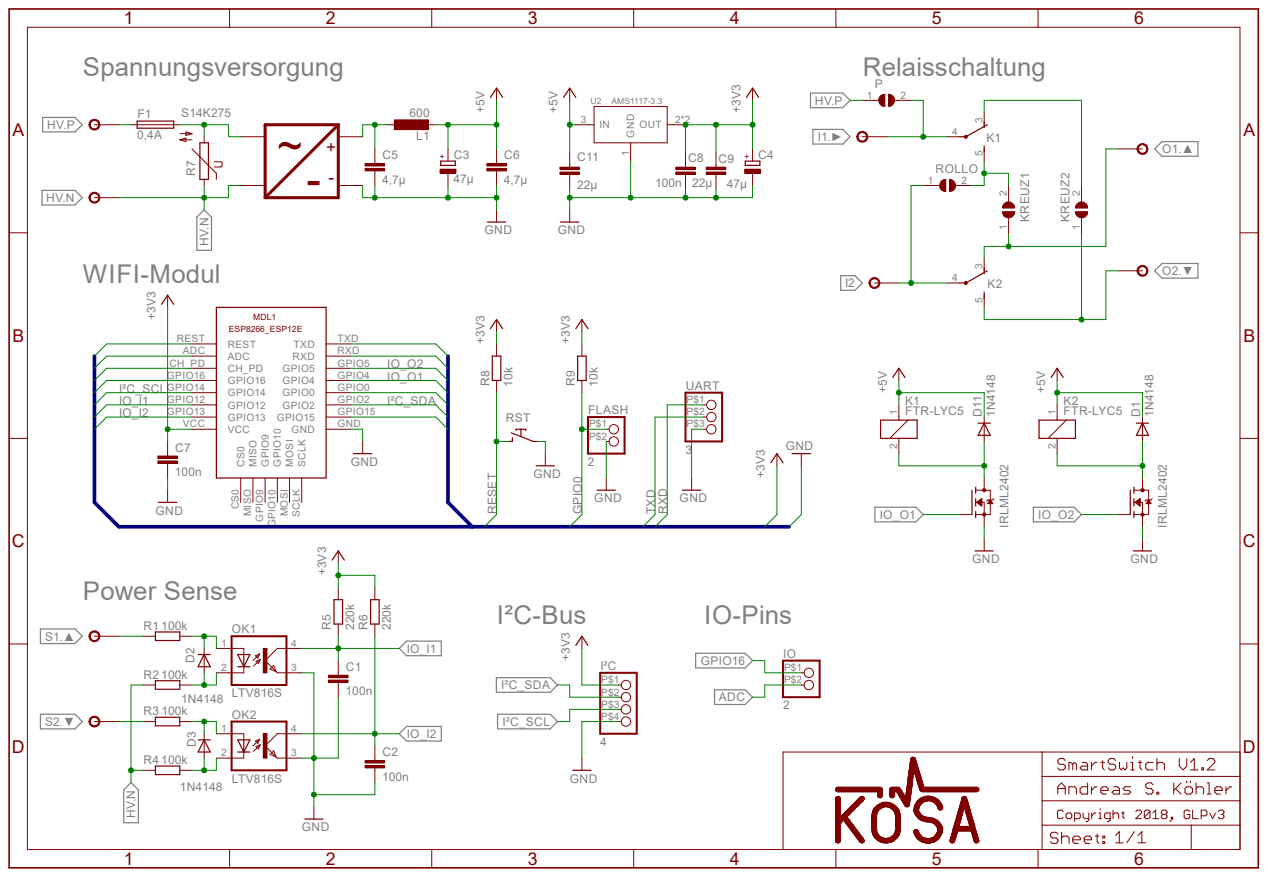
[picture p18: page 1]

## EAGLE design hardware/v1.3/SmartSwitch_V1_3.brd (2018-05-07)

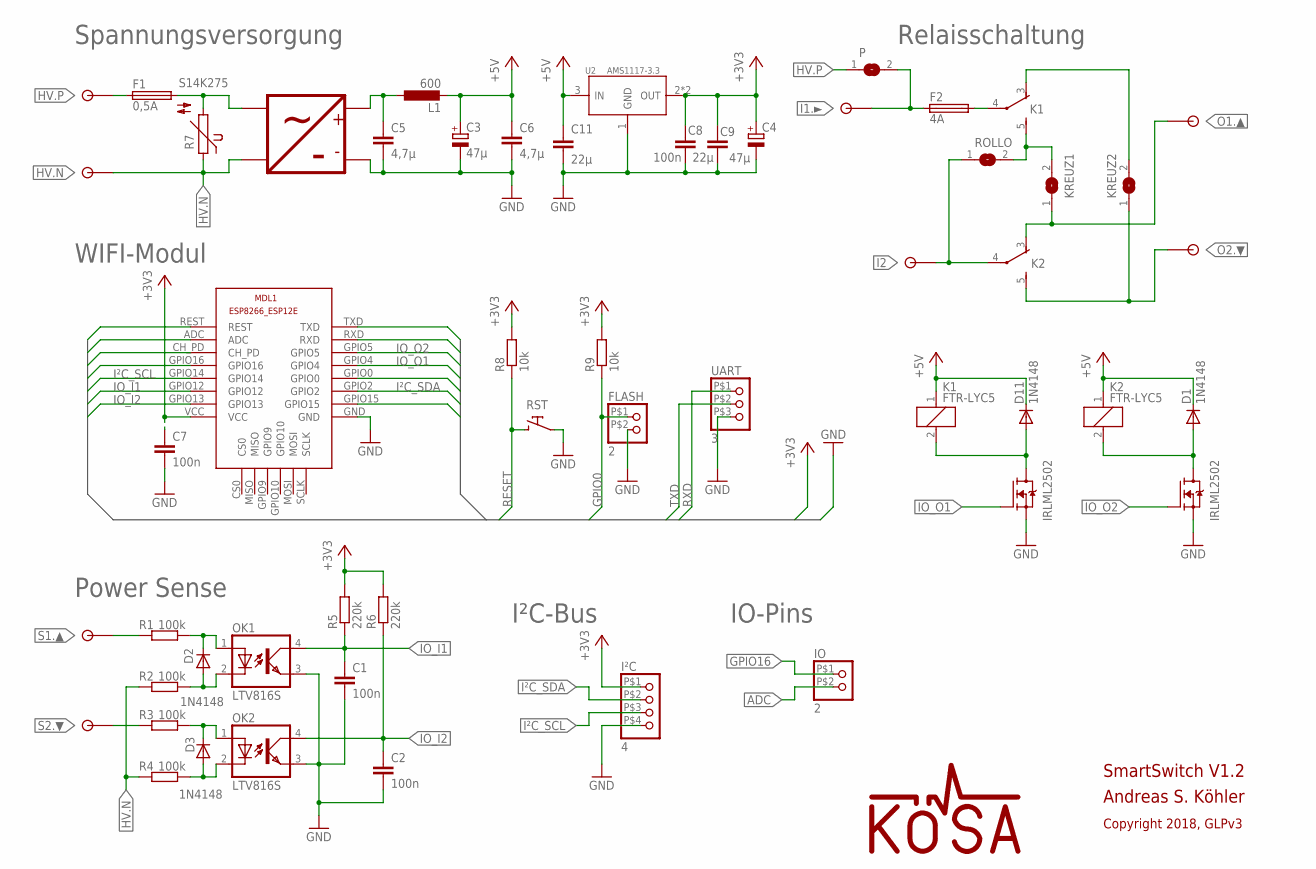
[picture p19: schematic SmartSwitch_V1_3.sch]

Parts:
C1, C2, C7, C8: 100n; C0805
C3, C4: 47µ; E2-5
C5, C6: 4,7µ; C0805
C9, C11: 22µ; C0805
D1, D2, D3, D11: 1N4148; SOD323-W
F1: 0,5A; SMD_FUSE_HOLDER
F2: 4A; SMD_FUSE_HOLDER
FLASH: 2; 1X02_SMALL
IO: 2; 1X02_SMALL
I²C: 4; 1X04_SMALL
K1, K2: FTR-LYC5; FTR-LYC
KREUZ1, KREUZ2: SJW
L1: 600; L3225P
MDL1: 1; ESP8266-ESP12E
OK1, OK2: LTV816S; SMD4
P: SJW
R1, R2, R3, R4: 100k; R1206
R5, R6: 220k; R1206
R7: S14K275; S14K275_
R8, R9: 10k; R1206
ROLLO: SJW
RST: SMD-TASTER_REICHELT_KMR_231_G_LFS
U2: AMS1117-3.3; SOT-223
U$1: HLK-PM01
U$2, U$3, U$4, U$5: RND_205-00276; RND205-00276
U$7, U$8: IRLML2502; SOT23
UART: 3; 1X03_SMALL

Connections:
+3V3: C4.+, C7.1, C8.1, C9.1, I²C.P$1 (1), MDL1.CH_PD, MDL1.VCC, R5.2, R6.2, R8.2, R9.2, U2.2 (OUT), U2.TER (OUT)
+5V: C3.+, C6.1, C11.1, D1.C, D11.C, K1.1, K2.1, L1.2, U2.3 (IN)
ADC: IO.P$2 (2), MDL1.ADC
GND: C1.2, C2.2, C3.-, C4.-, C5.2, C6.2, C7.2, C8.2, C9.2, C11.2, FLASH.P$2 (2), I²C.P$4 (4), MDL1.GND, MDL1.GPIO15, OK1.3 (EMIT), OK2.3 (EMIT), RST.1_1 (A), RST.1_2 (A), U2.1 (GND), U$1.DC-, U$7.2 (S), U$8.2 (S), UART.P$3 (3)
GPIO0: FLASH.P$1 (1), MDL1.GPIO0, R9.1
GPIO16: IO.P$1 (1), MDL1.GPIO16
HV.N: R2.1, R4.1, R7.1, U$1.AC2, U$2.P$2
HV.P: F1.P$1 (1), P.1, U$2.P$1
I1.►: F2.P$1 (1), P.2, U$4.P$1
I2: K2.4, ROLLO.1, U$3.P$1
IO_I1: C1.1, MDL1.GPIO12, OK1.4 (COL), R5.1
IO_I2: C2.1, MDL1.GPIO13, OK2.4 (COL), R6.1
IO_O1: MDL1.GPIO4, U$7.1 (G)
IO_O2: MDL1.GPIO5, U$8.1 (G)
I²C_SCL: I²C.P$3 (3), MDL1.GPIO14
I²C_SDA: I²C.P$2 (2), MDL1.GPIO2
unnamed: F2.P$2 (2), K1.4
unnamed: K1.5 (S), KREUZ1.2, ROLLO.2
unnamed: K1.3 (O), KREUZ2.2
unnamed: C5.1, L1.1, U$1.DC+
unnamed: F1.P$2 (2), R7.2, U$1.AC1
unnamed: D2.C, OK1.1 (A), R1.2
unnamed: D3.C, OK2.1 (A), R3.2
unnamed: D2.A, OK1.2 (C), R2.2
unnamed: D3.A, OK2.2 (C), R4.2
unnamed: D11.A, K1.2, U$7.3 (D)
unnamed: D1.A, K2.2, U$8.3 (D)
O1.▲: K2.3 (O), KREUZ1.1, U$3.P$2
O2.▼: K2.5 (S), KREUZ2.1, U$4.P$2
RESET: MDL1.REST, R8.1, RST.2_1 (B), RST.2_2 (B)
RXD: MDL1.RXD, UART.P$1 (1)
S1.▲: R1.1, U$5.P$2
S2.▼: R3.1, U$5.P$1
TXD: MDL1.TXD, UART.P$2 (2)

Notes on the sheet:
Spannungsversorgung
Power Sense
Relaisschaltung
WIFI-Modul
I²C-Bus
IO-Pins
SmartSwitch V1.2
Andreas S. Köhler
Copyright 2018, GLPv3

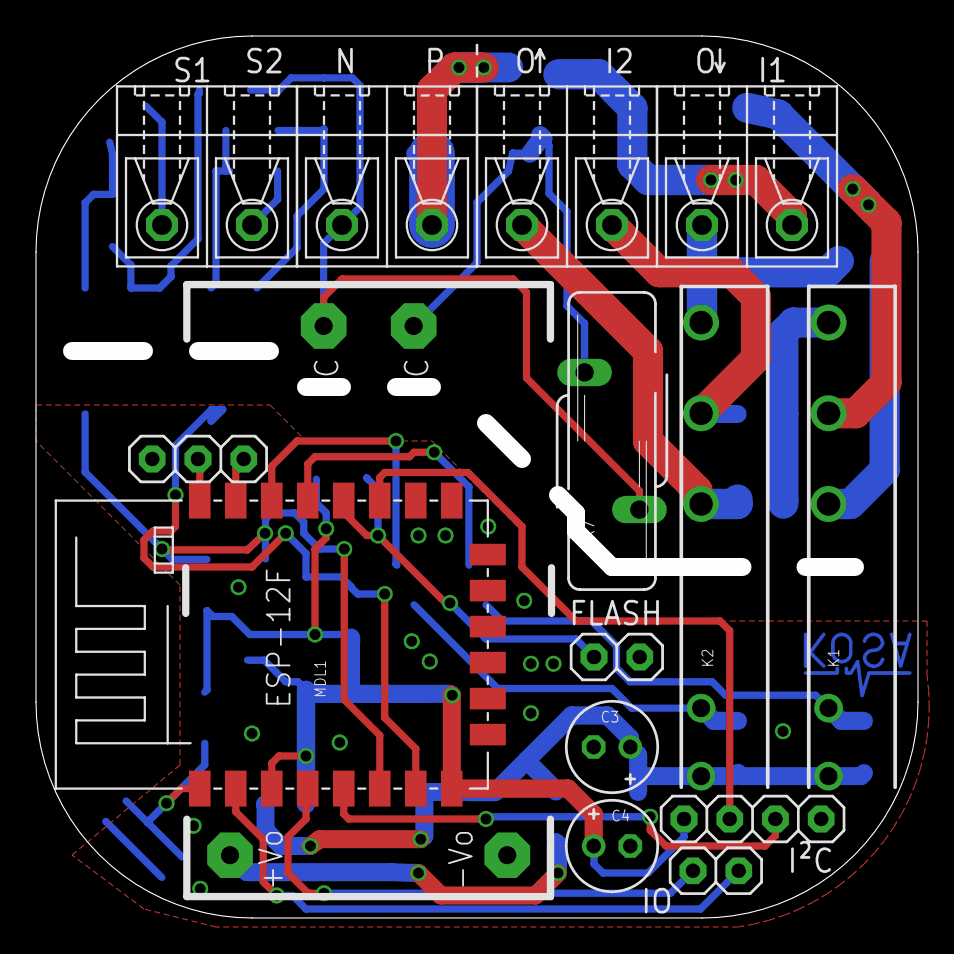
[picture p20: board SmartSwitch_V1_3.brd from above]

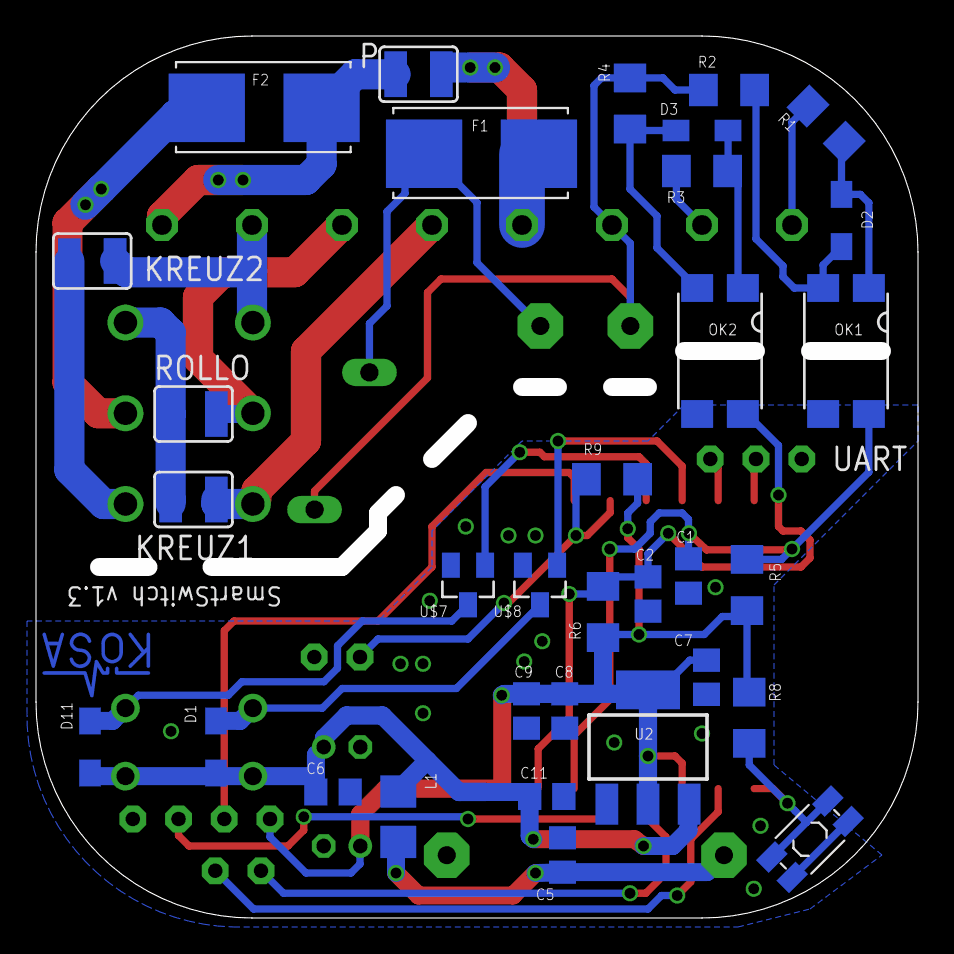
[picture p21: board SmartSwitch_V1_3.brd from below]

Board: 2 copper layers, 49.0 x 49.0 mm, 48 parts (33 on the bottom side), 34 nets.

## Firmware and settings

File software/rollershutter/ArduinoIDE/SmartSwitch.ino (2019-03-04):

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
// ##############################################################################################################################################################################
// ### Functions of SmartSwitch                                                                                                                                               ###
// ###                                                                                                                                                                        ###
// ###                                                                                                                                                                        ###
// ### + Built-in Enduser Setup to setup WiFi settings (initial operation)                                                                                                    ###
// ###   Configuration of MQTT-Broker-IP and Usage-Site also via Enduser Setup possible                                                                                       ###
// ###                                                                                                                                                                        ###
// ### + Built-in MQTT-Client                                                                                                                                                 ###
// ###   - MQTT-Topics:                                                                                                                                                       ###
// ###     * /SmartSwitch/<name/MAC>/status/position/      => Publish:   Actual position (in percent) of shutter                                                              ###
// ###     * /SmartSwitch/<name/MAC>/status/rssi/          => Publish:   RSSI of connected Accesspoint in dBm                                                                 ###
// ###     * /SmartSwitch/<name/MAC>/command/              => Subscribe: Subscribe-Topic of the Module                                                                        ###
// ###   - Instructionset:                                                                                                                                                    ###
// ###     * /UP:             => Opens the shutter completely                                                                                                                 ###
// ###     * /DOWN:           => Closes the shutter completely                                                                                                                ###
// ###     * /STOP:           => Stops the shutter at current position and publish act. position of shutter and RSSI of AP via MQTT                                           ###
// ###     * /TEACH:          => Starts Teaching-Mode to teach time to completely open/close shutter                                                                          ###
// ###     * /STATUS:         => Publishes act. position of shutter, RSSI of connected AP and Software-Revision via MQTT                                                      ###
// ##      * /SETUP:          => Deletes stored SSID and PW of already connected AP, do SW-Reset and boots into Enduser Setup                                                 ###
// ###     * /MANUAL_START:   => Starts Manual-Mode (Shutter can be moved without any restictions                                                                             ###
// ###     * /MANUAL_STOP:    => Stops Manual-Mode                                                                                                                            ###
// ###     * /<%-Value>:      => Moves Shutter to percentage position                                                                                                         ###
// ###                                                                                                                                                                        ###
// ### + Operation via Push-Buttons                                                                                                                                           ###
// ###   - Short push:            Move shutter in corresponding End-Position                                                                                                  ###
// ###   - Long push:             Move shutter as long as button is pushed (> 1s)                                                                                             ###
// ###   - Push during movement:  Stops motor (also if MQTT-Instruction was received during motion)                                                                           ###
// ###                                                                                                                                                                        ###
// ### + Built-in Arduino OTA flashing interface (Firmwareupdate via WiFi)                                                                                                    ###
// ##############################################################################################################################################################################

// *** Needed Libraries *********************************************************************************************************************************************************
#include <ESP8266WiFi.h>                                                              // Library for ESP8266
#include <WiFiClient.h>                                                               // Library for WiFi-Client
#include <EEPROM.h>                                                                   // Library for EEPROM-Usage
#include <WiFiManager.h>                                                              // Library for WiFi-Manager
#include <ArduinoOTA.h>                                                               // Library for OTA-Updating
#include <ESP8266mDNS.h>                                                              // Library for mDNS-Usage
#include <WiFiUdp.h>                                                                  // Library for UDP-Communication
#include <PubSubClient.h>                                                             // Library for MQTT-Handling
extern "C" {
  #include "user_interface.h"                                                         // Include Espressif Library
}
// *** Needed Variables *********************************************************************************************************************************************************
String MQTT_name;                                                                     // Variable (String) to store name of MQTT-Client
char MQTT_name_char[128];                                                             // Name (Char) to connect MQTT-Client with broker
String hostname;                                                                      // Variable for Name of Module (part of MQTT-Topic, either IP of module or stored site) 
String topic = "/SmartSwitch/";                                                       // First part of MQTT-Topic for publishing                *** Part of MQTT-Topic for publishing ***
int WiFiManagerTimeout = 180;                                                         // Define Timeout for Wifi-Manager and set it to 180s     *** Timeout for WiFi-Manager          ***
char MQTT_BROKER[40] = "192.168.2.115";                                               // Preset IP of MQTT-Broker                               *** Preset-IP of MQTT-Broker          ***
bool wifiFirstConnected = false;                                                      // Flag for first WiFi connection
int cf = 0;                                                                           // WiFi Connection flag
String ausgabe;                                                                       // Variable for MQTT-Message
String top;                                                                           // Variable to combine Strings for Topic-String
char hostname_char[140];                                                              // Variable for MQTT-Hostname
bool shouldSaveConfig = false;                                                        // Flag for saving MQTT-Config
char site[128];                                                                       // Variable for Usage-Site
char broker[40];                                                                      // Variable for MQTT-Broker address
char MQTTget_message[128];                                                            // Variable for incoming MQTT-Messages
String MQTTget_topic;                                                                 // Variable for topic of incoming MQTT-Messages
unsigned long lastReconnectAttempt = 0;                                               // Timer-Variable for MQTT-Reconnection
bool newMQTTmessage = false;                                                          // Flag if new MQTT-Message is avaliable
bool drive = false;                                                                   // Flag if shutter is in motion 
bool manual_flag = false;                                                             // Flag for manual motion
unsigned int down_time = 0;                                                           // Variable for teached Down-Time
unsigned int up_time = 0;                                                             // Variable for teached Up-Time
float pos = 0;                                                                        // Variable for actual position
float pos_fb = 0;                                                                     // Variable to calculate position to be feedbacked to MQTT-Network
unsigned long MovedTime = 0;                                                          // Variable for time, beeing in motion
unsigned long StartMoveTime = 0;                                                      // Variable for Motion-Start-Time
unsigned long StartPosCalcTime = 0;                                                   // Variable for Start-Time to calcualte position
bool moving_up = false;                                                               // Flag for Up-Movement
bool moving_down = false;                                                             // Flag for Down-Movement
bool teach_flag = false;                                                              // Flag for Teaching-Mode
bool percentage = false;                                                              // Flag for motion according percentage target value
int delta = 0;                                                                        // Variable for Position-Delta (now/target)
int soll = 0;                                                                         // Variable for target position
bool up_pressed = false;                                                              // Flag if UP was pressed
bool down_pressed = false;                                                            // Flag if DOWN was pressed
unsigned long LastTime = 0;                                                           // Variable to store last time of meassurement
unsigned long CurrentTime = 0;                                                        // Variable to store actual time
unsigned long interval = 1000;                                                        // Variable to store interval of MQTT-Connection-Check    *** Interval of MQTT-Check   ***
String ProgRevision = "SmartSwitch V1.2";                                             // Variable to store Software-Revision                    *** Software-Revision        ***
// *** Needed IOs ***************************************************************************************************************************************************************
#define IO_I1 12                                                                      // Map IO_I1 (Input: UP) to GPIO12
#define IO_I2 13                                                                      // Map IO_I2 (Input: DOWN) to GPIO13
#define IO_O1 4                                                                       // Map IO_O1 (Relais: DIRECTION) to GPIO4
#define IO_O2 5                                                                       // Map IO_O2 (Relais: POWER) to GPIO5
// *** Needed Services **********************************************************************************************************************************************************
WiFiClient espClient;                                                                 // Create a WiFi-Client
PubSubClient client(espClient);                                                       // Create a PubSubClient-Object (MQTT)

// ##############################################################################################################################################################################
// ### Calback for Wifi got IP ##################################################################################################################################################
// ##############################################################################################################################################################################
void onSTAGotIP (WiFiEventStationModeGotIP ipInfo) {                                  // Callback if WiFi connection is established and IP gotten
  wifiFirstConnected = true;                                                          // Set flag
}

// ##############################################################################################################################################################################
// ### Callback for MQTT-Message get ############################################################################################################################################
// ##############################################################################################################################################################################
void mqtt_callback(char* topic, byte* payload, unsigned int length) {
  Serial.print("Message arrived [");                                                  // Debug printing Topic
  Serial.print(topic);
  Serial.print("]: ");
  for (int i = 0; i < 128; i++) {                                                     // Initialize Char-Array for new message
    MQTTget_message[i] = 0;                                                           // Make it empty
  }
  for (int i = 0; i < length; i++) {                                                  // For lenght of new MQTT-Message
    MQTTget_message[i] = (char)payload[i];                                            // Get payload of MQTT-Message to Char-Array
    Serial.print((char)payload[i]);                                                   // Debug printing
  }
  Serial.println();
  MQTTget_topic = topic;                                                              // Store MQTT-Topic to variable
  newMQTTmessage = true;                                                              // Set flag for new MQTT-Message
}

// ##############################################################################################################################################################################
// ### If MQTT-Client isn't connected => reconnect! #############################################################################################################################
// ##############################################################################################################################################################################
boolean reconnect() {
  MQTT_name = "SmartSwitch_" + String(WiFi.macAddress());                             // Define name of MQTT-Client (SmartSwitch_XX:XX:XX:XX:XX:XX:XX:XX)
  if (client.connect(MQTT_name.c_str())) {                                            // Connect to MQTT-Broker
    ausgabe = "Connected";                                                            // Build strings to send to MQTT-Broker and send it
    top = topic + hostname_char + "/status/";                                         // Built topic to sent message to
    client.publish(top.c_str(), ausgabe.c_str());                                     // Publish MQTT-Message
    top = topic + hostname_char + "/command/";                                        // Built topic to sent message to
    Serial.println("TOPIC: " + top);                                                  // Debug printing
    client.subscribe(top.c_str());                                                    // Subscribe to MQTT-Topic
    return true;                                                                      // If connection is established, return true
  } else {
    Serial.print("failed, rc=");                                                      // In case of no connection:
    Serial.println(client.state());                                                   // Debug print
    return false;                                                                     // If connection isn't established, return false
  }
}

// ##############################################################################################################################################################################
// ### Callback for Wifi Config Mode ############################################################################################################################################
// ##############################################################################################################################################################################
void configModeCallback (WiFiManager *myWiFiManager) {                                // Callback if WiFi-Manager enters config mode
    Serial.println("Entered config mode");                                            // Debug printing
    Serial.println(WiFi.softAPIP());
    Serial.println(myWiFiManager->getConfigPortalSSID());
}

// ##############################################################################################################################################################################
// ### Callback for to save parameters from WIFI-Manager ########################################################################################################################
// ##############################################################################################################################################################################
void saveConfigCallback () {
  Serial.println("Should save config");                                               // Debug printing
  shouldSaveConfig = true;                                                            // Set flag to store config (MQTT)
}
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
void loop() {
  ArduinoOTA.handle();                                                                // Start OTA-Handle
  if (!client.connected()) {                                                          // If MQTT-Client isn't conntected to broker
    MQTT_reconnect();                                                                 // Reconnect to MQTT-Broker
  } else {                                                                            // If connected to MQTT-Broker  
    if (newMQTTmessage) {                                                             // If new MQTT-Message avaliable
      newMQTTmessage = false;                                                         // Reset "New-MQTT-Message-Flag"
      MQTT_Handling();                                                                // Call MQTT-Handling
    }
  }
  ButtonHandling();                                                                   // Call Button-Handling Routine
  MoveNow();                                                                          // Call Move-According-Time Routine
  CurrentTime = millis();                                                             // Get current time
  if ((CurrentTime - LastTime) >= interval) {                                         // Wait interval-time until checking MQTT-Connection
    LastTime = CurrentTime;
    client.loop();
  }
}

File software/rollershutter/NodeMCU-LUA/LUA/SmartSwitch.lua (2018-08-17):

--------------------------------------------------------------------------------------------------------------------------------------
--------------------------------------------------------------------------------------------------------------------------------------
----- SmartSwitch.lua              ---------------------------------------------------------------------------------------------------
----- Mainprogram for SmartSwitch  ---------------------------------------------------------------------------------------------------
----- Copyright © 2018 A. Köhler   ---------------------------------------------------------------------------------------------------
-----																		----------------------------------------------------------
----- This program is free software: you can redistribute it and/or modify	----------------------------------------------------------
----- it under the terms of the GNU General Public License as published by	----------------------------------------------------------
----- the Free Software Foundation, either version 3 of the License, or		----------------------------------------------------------
----- (at your option) any later version.									----------------------------------------------------------
-----																		----------------------------------------------------------
----- This program is distributed in the hope that it will be useful,		----------------------------------------------------------
----- but WITHOUT ANY WARRANTY; without even the implied warranty of		----------------------------------------------------------
----- MERCHANTABILITY or FITNESS FOR A PARTICULAR PURPOSE.  See the			----------------------------------------------------------
----- GNU General Public License for more details.							----------------------------------------------------------
-----																		----------------------------------------------------------
----- You should have received a copy of the GNU General Public License		----------------------------------------------------------
----- along with this program.  If not, see <http://www.gnu.org/licenses/>.	----------------------------------------------------------
--------------------------------------------------------------------------------------------------------------------------------------
--------------------------------------------------------------------------------------------------------------------------------------

--------------------------------------------------------------------------------------------------------------------------------------
-- MQTT-Handler ----------------------------------------------------------------------------------------------------------------------
--------------------------------------------------------------------------------------------------------------------------------------
function message_get(topic, data)
-- Handling to Stop during automatic drive -------------------------------------------------------------------------------------------
	if fahren == 1 then                                                 -- During movement, a interrupt should stop the motor
        motionStop()                                                    -- Stop shutter
        tmr.unregister(5)                                               -- Stop timer for half-automatic movement of shutter
		tmr.unregister(4)												-- Reset Movement-Flag
        fahren = 0                                                      -- Set movement-Flag "off"
        tmr.delay(500000)												-- Stop program for 500ms
    end 
-- Handling if "UP" was received -----------------------------------------------------------------------------------------------------
    if data == "UP" then
        if position <= 0 then                                           -- If shutter is already completely opened
            position = 0                                                -- Set position to 0%
            return                                                      -- Return
        end
        moveUp()
        fahren = 1                                                    	-- Set Movement-Flag
        tmr.alarm(4, 100, tmr.ALARM_AUTO, function()                	-- Calculate new position every 100ms
            position = position - (100 / up_time)
        end)
        tmr.alarm(5, (100 * (up_time / 100) * position) + 3000, tmr.ALARM_SINGLE, function() -- move downward calculated time to reach position = 0% (3s longer to open completly for shure)
            tmr.unregister(4)                                       	-- Stop calculation of position
            position = 0                                            	-- Set position to 0%
            motionStop()                                            	-- Stop movement
            fahren = 0                                              	-- Reset Movement-Flag
        end)
    end
-- Handling if "DOWN" was received ---------------------------------------------------------------------------------------------------
    if data == "DOWN" then
        if position >= 100 then                                         -- If shutter already completly closed 
            position = 100                                              -- Set position to 100 %
            return                                                      -- Return
        end
        moveDown()
        fahren = 1                                                    	-- Set Movement-Flag
        tmr.alarm(4, 100, tmr.ALARM_AUTO, function()                	-- Calculate new position every 100ms
            position = position + (100 / down_time)
        end)
        tmr.alarm(5, (100 * (down_time / 100) * (100 - position)) + 3000, tmr.ALARM_SINGLE, function()   -- move downward calculated time to reach position = 100 % (3s longer to close completly for shure)
            tmr.unregister(4)                                       	-- Stop calculation of position
            position = 100                                          	-- Set position to 100%
            motionStop()                                            	-- Stop movement
            fahren = 0                                              	-- Reset Movement-Flag
        end)
    end
-- Handling if "STOP" was received ---------------------------------------------------------------------------------------------------    
	if data == "STOP" then
        motionStop()                                                    -- Stop shutter
        tmr.unregister(5)                                               -- Stop timer for half-automatic movement of shutter
		tmr.unregister(4)												-- Reset Movement-Flag
        fahren = 0                                                      -- Set movement-Flag "off"
    end
-- Handling if "TEACH" was received ---------------------------------------------------------------------------------------------------    
	if data == "TEACH" then
		teach_flag = 1
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

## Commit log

2018-08-17 BugFix
    BugFix to guarantee complete opening or closing with UP/DOWN command.
    Opening / Closing will last 3s longer than actual teached time.
    [SmartSwitch.lua]
2018-09-04 added Reichelt part url link
    [BOM SmartSwitch with Supplierlinks.xls]
2018-09-26 Equalization of BOM and Schematic
    Mixup of "my" standard driver transistor (IRLML2502, 20V 4,2A) and the used one (IRLML2402, 20V, 1,2A) was adjusted.
    Both will work in the given circuit becaus only a coil-current of 35mA is necessary.
    [SmartSwitch_V1_3.sch]
2019-01-30 Software now avaliable for ArduinoIDE
    Additional software for ArduinoIDE avaliable:
    - Extended Endusersetup (including Site- and MQTT-Configuration)
    - OTA-Update possible
2019-01-31 BugFix
    - Operation via Push-Buttons should also be possible if MQTT-Connection is broken
    - Reasonable displaying of "site" and "broker" in WiFiManager during first initialisation
    [SmartSwitch.ino]
2019-01-31 ADD: Instructionset for Arduino-Sketch
2019-02-03 BugFix (If EEPROM-Content isn't a number...)
    After first initialisazion and bootup of the module, the EEPROM-Content isn't defined.
    Because of the fact that the content will be read, the Software gets a "nan" error.
    Now there is a errorhandling if one of the variables in EEPROM isn't a number.
    [SmartSwitch.ino]
2019-03-04 BugFix - Retaining position, extended status messages
    [SmartSwitch.ino]

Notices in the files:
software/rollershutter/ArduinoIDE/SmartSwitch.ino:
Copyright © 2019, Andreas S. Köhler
